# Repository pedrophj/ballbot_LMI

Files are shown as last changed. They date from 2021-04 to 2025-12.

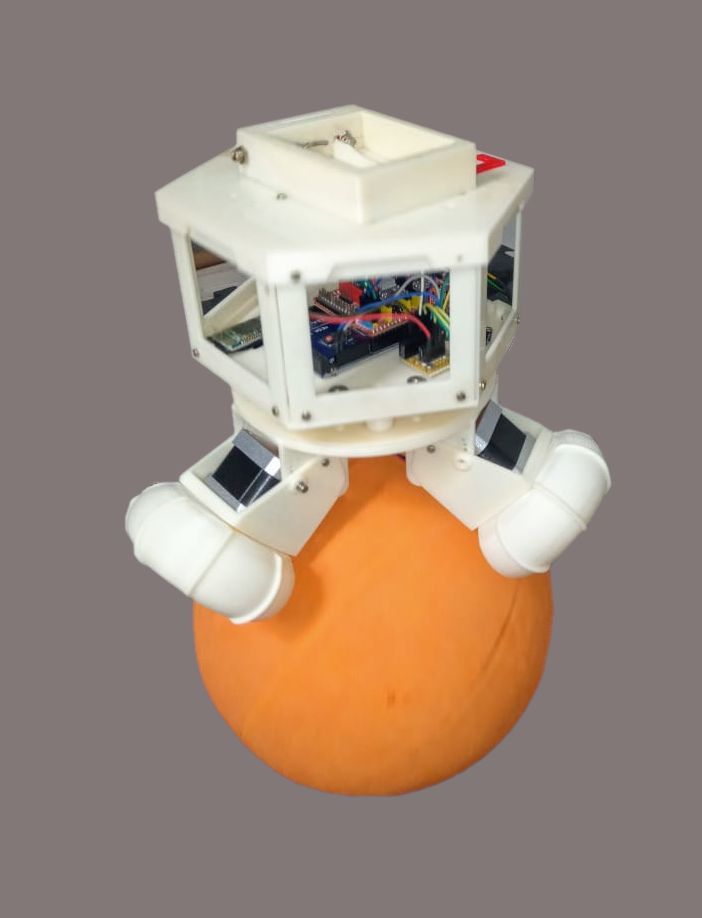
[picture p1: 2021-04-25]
MATLAB Simulink/ballbot_LMI.png

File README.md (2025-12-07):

# Design and Experimental Validation of a Ballbot: A Self-balancing Omnidirectional Robot

**Author**: Pedro Henrique de Jesus (pedro.jesus@sp.senai.br), ITA / SENAI 

**Advisors**: Cairo L. Nascimento Jr. (cairo@ita.br), Douglas Soares dos Santos (dsoares@ita.br), ITA.

## Abstract:
The files and codes presented in this repository refer to the construction of the ballbot robot. This robot rides on top of a basketball, and falls into a recent category of omnidirectional robots. In addition to the construction, files are available for the implementation of the camera location system, autonomous waypoint navigation and object tracking system.

ballbot 2

## Prerequisites for running MATLAB files:
- MATLAB R2015a

## Prerequisites for recording the embedded system:
- Arduino IDE equal to or greater than version 1.8.7
- Arduino Mega board

## Prerequisites for running the files in Python:
- Python 3.5.2 or higher
- numpy package installed with version 1.17.3 or higher
- OpenCV package installed with version 4.1.1.26 or higher

## Prerequisites for running the ballbot in the 3D simulator:
- CoppeliaSim version greater than or equal to 4.1.1

## File organization
- Files for 3D printing
  - Folder: mechanical
- Simulators
  - Folders: MATLAB Simulink and 3D simulator
- Embedded system
  - Folder: Arduino program
- Software for autonomous waypoint navigation
  - Folder: Control software
- Videos of real experiments and simulation
  - Folder: Videos
- My_Publications
  - Dissertação_Ballbot_Pedro_HJ.pdf: PDF of the master's dissertation
  - Artigo SysCon 2024: Design and Experimental Validation of a Ballbot: A Self-balancing Omnidirectional Robot.pdf
  - Folder: Presentation

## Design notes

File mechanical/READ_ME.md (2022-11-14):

List of printable files

To print a ballbot structure:
    
    Number          File 
      1             robo_tampaInferior.stl
      1             robo_tampaSuperior.stl
      1             robo_disco.stl
      6             robo_janela.stl
      3             robo_suporteMotor.stl
      3             robo_suporteMotorDisco.stl
      3             robo_paralama.stl
      3             robo_apoioDisco.stl
      
To print a ballbot wheel:
    
    Number          File 
      6             roda_roleteMenor.stl
      6             roda_roleteMaior.stl
      1             roda_garfo.stl
      1             roda_disco.STL
      1             roda_discoMotor.STL

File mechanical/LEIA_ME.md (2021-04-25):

Lista de arquivos para impressão.

	Para imprimir uma estrutura do ballbot:
    
    Quantidade      Arquivo 
      1             robo_tampaInferior.stl
      1             robo_tampaSuperior.stl
      1             robo_disco.stl
      6             robo_janela.stl
      3             robo_suporteMotor.stl
      3             robo_suporteMotorDisco.stl
      3             robo_paralama.stl
      3             robo_apoioDisco.stl
      
    Para imprimir uma roda do ballbot:
    
    Quantidade      Arquivo 
      6             roda_roleteMenor.stl
      6             roda_roleteMaior.stl
      1             roda_garfo.stl
      1             roda_disco.STL
      1             roda_discoMotor.STL

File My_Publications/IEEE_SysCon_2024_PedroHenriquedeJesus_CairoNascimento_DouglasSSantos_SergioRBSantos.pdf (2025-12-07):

# Design and Experimental Validation of a Ballbot: A Self-balancing Omnidirectional Robot

Pedro Henrique de Jesus∗
, Cairo Lucio Nascimento J ´ | unior ´

†
,
Douglas Soares dos Santos†
, Sergio Ronaldo Barros dos Santos ´

‡
∗ Servic¸o Nacional de Aprendizagem Industrial (SENAI), Pindamonhangaba-SP, Brazil Email: pedro.jesus@sp.senai.br
†
Instituto Tecnologico de Aerona ´ | utica (ITA), S ´ | ao Jos ˜ | e dos Campos-SP, Brazil ´
Emails: {cairo, dsoares}@ita.br
‡ Universidade Federal de Sao Paulo (UNIFESP), S ˜ | ao Jos ˜ | e dos Campos-SP, Brazil ´
Email: sergio.ronaldo@unifesp.br

Abstract—This article presents the design, modelling and control of a Self-balancing Omnidirecional Robot, also known as ballbot, for performing autonomous navigation (path following) and object tracking in structured environments using vision feedback. A real ballbot has unstable and non-linear dynamics with second-order constraints, and is classified as an underactuated system. These features require the implementation of a robust and efficient embedded control system for allowing the realization of attitude and navigation control. In this context, the development of this work was divided into six stages: 1) design and mechanical construction of the omnidirectional wheels and chassis using a 3D printer; 2) mathematical modeling of the prototype developed in Matlab/Simulink and creation of a realistic simulated model in CoppeliaSim simulator; 3) design of LQR and P/PI controllers to control X and Y position and orientation respectively using the mathematical model; 4) evaluation of designed controllers using the realistic model developed; 5) implementation of the controllers in the embedded system and integration with inertial sensors and actuators; 6) experimental validation of the proposed control system for autonomous navigation and object tracking. The experimental results have shown that the developed ballbot is able to perform path following and object tracking efficiently.

I. INTRODUCTION

A Self-balacing Omnidirectional Robot (Ballbot) is a mobile robot that incorporates the characteristics observed in an inverted pendulum which is balanced and moved on top of a sphere [1].
A Ballbot has numerous potential applications in several sectors of our society, such as working cooperatively in domestic and industrial environments transporting loads, acting as an information assistant in malls and hospitals, assisting senior citizens in sit-to-stand and walking movements, guiding leading visually impaired people in an unknown environments, autonomously mapping outdoor and indoor environments, performing mobile target tracking, and remote monitoring of large facilities.
One of the first ballbots was created in 2005 specifically to study the problem of dynamically unstable robots with a single point of contact with the ground [2]. The ballbot might carry out agile movements due to the ball rolling action and has inherently nonlinear unstable dynamics caused by the inverted pendulum. Unlike statically stable robots, dynamically unstable robots can accelerate and decelerate quickly and suffer a greater influence of gravity. This feature requires that the control system should effectively deal with the instability and nonlinearities that exist in this type of robot [3].
However, since a ballbot has unstable and nonlinear dynamics with second-order constraints and is classified as an underactuated system, designing effective attitude and navigation controllers for it is definitelynot a trivial task [4], [5]. This work aims to describe the development phases for designing, modeling and control of a ballbot used to perform autonomous navigation and object tracking in structured environments using inertial and vision sensors.
Initially, the robot chassis and its omnidirectional wheels were built using a 3D printer. Considering the robot physical parameters, including the power limitation of the motor drive power, 2 simulation models were developed: a mathematical model for Matlab/Simulink and a more realistic model for the CopelliaSim robot simulator. Using the mathematical model, the LQR and P/PI controllers were designed and tuned to control X and Y robot speed/position and orientation. Then they were evaluated using the realistic model in CoppeliaSim. For autonomous navigation, the ballbot receives its 3D position computed by an external vision system allowing it to follow the desired path defined by a set of waypoints positioned in its environment. For object tracking the ballbot uses an embedded camera to detect and locate the target object in relation to its own position. Then the vision based controller uses this informationto generate the control signals to the wheel actuators.
The main contribution of this work is to present a methodology for the construction of a ballbot, from the mechanical aspects to the implementation of the autonomous navigation and object tracking algorithms, including the experimental validation. The algorithms developed for this work and some demonstration videos are publicly available at https://github.com/pedrophj/ballbot LMI.
This article is organized as follows. Section II details the 2D model of the ballbot, as well as the parameters of the 3D simulation. Section III describes the methodology, constructive
2024 IEEE International Systems Conference (SysCon) | 979-8-3503-5880-3/24/$31.00 ©2024 IEEE | DOI: 10.1109/SysCon61195.2024.10553418

Authorized licensed use limited to: ITA - Instituto Tecnológico de Aeronáutica. Downloaded on August 19,2024 at 15:56:12 UTC from IEEE Xplore. Restrictions apply.

aspects and the control architecture. Simulation results for autonomous navigation and object tracking are presented in Section IV. And finally, conclusion and future works are described in Section V .

A. Related Works

In the last years, several studies were carried out for improving the stabilization control design of the self-balancing omnidirectional robot; however some few works present the complete stages of development of a ballbot, that goes from its mechanical structure to the implementation of the embedded control and guidance systems, allowing a full autonomous navigation and object tracking in indoor environments. Considering the existing literature about the path tracking and navigation, in the work of [6], the authors have only presented an attitude control for generating the velocity commands for the three wheels. In [7], a trajectory tracking approach based on waypoints for executing maneuver and avoiding collision with static and dynamic obstacles in cluttered environments is proposed. In [8], the authors have described an experimental trial to validate the control policies derived from the dynamic model and Dijsktra’s algorithm for surveillance and monitoring applications. In [9], a Fuzzy-based trajectory controller is proposed for performing the straight and circular motions in simulation. In [10], a Sliding Model Control (SMC) approach for trajectory tracking in simulation considering uncertainty and disturbance is proposed. In the [11], the authors have presented the design and implementation of a Fuzzy/PD controllers for controlling the attitude and tracking trajectories.
Regarding the mechanical and control system aspects, in the work of [12], the authors have presented the mechanical construction of a ballbot and modelling procedure using the Euler–Lagrange equations to derive the dynamic model. A Linear Quadratic Regulator with Integral (LQR + I) controller is proposed to keep the location around a point. In other work [5], the ballbot modeling and LQR controllers design to control the angular and X-Y position is proposed. However, the experimental validation is conducted using previously developed prototype.

II. BACKGROUND

In this section, we introduce all general aspects and some concepts employed throughout this work such as the used environment.

A. Ballbot Model

Figure 1 shows the simplified free body diagram of the ballbot represented by identical XZ and YZ planes. The free body diagram of the system is composed of a wheel (in orange), a rigid body (in blue) and a rod of length L used to connect the center of mass to the wheel. Note that X, Y and Z axes belongs to the inertial coordinate system whereas XB, YB and ZB axes composes the body coordinate system of the ballbot.

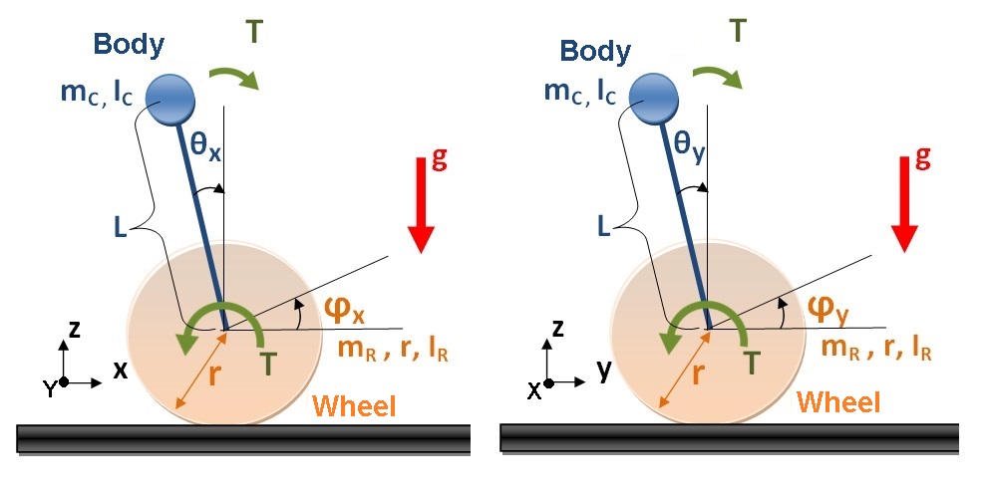
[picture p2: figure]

Fig. 1. Simplified ballbot planar model

Let be consider the angular acceleration on the sphere, wheel angle (φx) with respect to an initial horizontal reference point, and wheel angular velocity (φ˙x) as input of the simplified ballbot planar model and pitch (θx) angle measured in relation to the Y axis, angular velocity ( ˙θx) around the Y axis as output of the system. For describing the mathematical model, we use the parameters shown in Table I.
The nonlinear differential equations of the system is described in the form of a matrix as presented in eq. (1).

x˙1
x˙2
x˙3
x˙4

=

x2
mcgLsin(x1) + c1u + mcrLsin(x1)x

2
2
Ic + mcL

2 + mcrLcos(x1)
x4
−ru

(1)

where c1 = −Ir − (mr + mc)r

2 − mcrLcos(x1), u = φ¨, x1 = θx, x2 = ˙θ, x3 = x, and x4 = x˙.
It is assumed that the sphere is a rigid body and to be on contact with the ground without friction and slipping, and the wheel dynamics are disregarded due to their operation occurs at low angular speed.
The linearization of the nonlinear model is performed for an operating point that sets the angle change around the X and Y axes to be approximately zero. Thus, we can present the nonlinear ballbot plane model as a linear model in space states form.

x˙1
x˙2
x˙3
x˙4

=

0 1 0 0
24.84 0 0 0
0 | 0 0 1
0 | 0 0 0

x1
x2
x3
x4

+

0
−0.73
0
−0.12

u (2)

where x˙1, x˙2, x˙3 and x˙4 are the angular velocity observed on the body of the ballbot and u is the control signal.

B. Virtual Ballbot Model in CoppeliaSim
The simulator is an important tool for the control system design during the evaluation stage, since the system instability due to incorrect adjustment of the controllers might cause the ballbot to fall on the ground and consequently damage

TABLE I
PARAMETERS USED FOR MODELLING THE VIRTUAL BALLBOT
Parameter | Value | Unit
Acceleration of gravity | 9.81 | m/s²
Ball radius (r) | 0.12 | m
Ball mass (Mc) | 0.58 | kg
Moment of inertia of the sphere in X | 0.0134 | kgm²
Moment of inertia of the sphere in Y | 0.0134 | kgm²
Moment of inertia of the sphere in Z | 0.0134 | kgm²
Diameter of the cylindrical body | 0.2 | m
Height of the body (L) | 0.3 | m
body mass | 1.6 | kg
Moment of inertia of the body at X | 0.0413 | kgm²
Moment of inertia of the body in Y | 0.0413 | kgm²
Moment of inertia of the body in Z | 0.0720 | kgm²
Omniwheel diameter | 7 | cm
Omniwheel thickness | 1.3 | cm
Omniwheel mass | 50 | g
Omniwheel moment of inertia at X | 6.16 × 10⁻⁶ | kgm²
Omniwheel moment of inertia in Y | 6.16 × 10⁻⁶ | kgm²
Omniwheel moment of inertia in Z | 1.22 × 10⁻⁴ | kgm²

the actual prototype. In this work, we developed a virtual 3D model of the ballbot using the CoppeliaSim simulator to evaluate the performance of the stabilization and trajectory tracking controllers. This model reproduces the behavior of the dynamics observed in the real prototype with reliability and precision, taking into account disturbances such as wind and irregularities on the ground. Figure 2(a) shows the virtual ballbot developed for the CoppeliaSim simulator.
The attitude and position controllers are designed using the mathematical model described in Section II and are implemented in a script using the LUA language. This language allows to execute the control algorithms implemented in a script directly in CopelliaSim without using an external API. All the parameters shown in Table I are derived from the actual ballbot and are used to build the virtual model executed in CoppeliaSim. In CoppeliaSim each object in the scene can be edited separately, so that the dynamic properties of each part of the ballbot can be adjusted based on the values obtained from the prototype.

III. DEVELOPMENT OF THE SELF-BALANCING OMNIDIRECTIONAL ROBOT

A. Mechanical and Motor Aspects

The actual ballbot frame (Fig. 2(b)) is composed of a set of elements manufactured using a 3D printer and fixed using screws. The designed frame has a hexagonal shape with two layers for installing the on-board electronics, camera and battery. Each actuator is composed of a set of motor and omnidirectional wheel, positioned at 120º isometric angles and fixed to the frame using specifically designed supports. The positioning defined by the actuators allows eliminating non-holomonic movement restrictions, allowing the ballbot to execute displacement in X and Y directions (longitudinal and lateral movements) and around their own vertical axis.

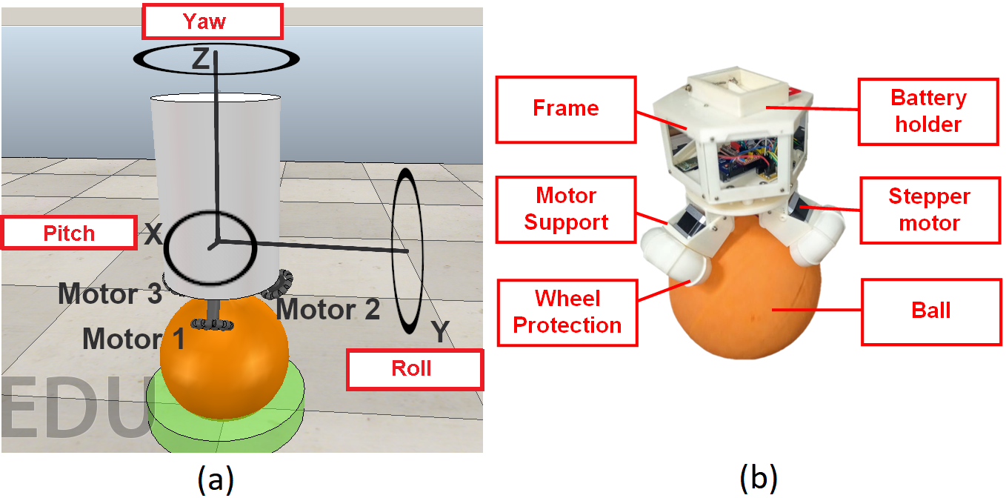
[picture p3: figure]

Fig. 2. Proposed actual and simulated Ballbot

(a) Model | (b) 3D printed

Fig. 3. Designed Omnidirecional Wheels

The motors are to be chosen to overcome the inertial imposed by the sphere, i.e., they must have enough torque to rotate the sphere producing an angular velocity that is translated into a linear velocity. The designed omnidirectional wheels (Fig. 3) have twelve 90 degree rollers symmetrically arranged to allow the ballbot to move along the Y axis and reduce body shake whereas conventional wheel rotation produces movement on the X axis.
The 4-wire bipolar stepper (NEMA 17, model 17HS4401) has 1.8 degree per step for smooth motion and requires a maximum current of 1.7A/phase for operation. This motor needs of 200 steps to complete a full 360 degree per turn and has a maximum load of 4.28 kg/cm. The angular speed of the motor depends on the frequency of the command generated by the drive in which affects the response of the platform to perform stabilization and holonomic displacement.
B. Embedded Electronics Systems

The ballbot uses a microcontroller (Arduino Mega) which it receives the acceleration and angular velocity measurements provided by the Inertial Measurement Unit (IMU) and the orientation given by the compass, and also generates the control signals of each of the motors through the drive DVR8825 composed of MOSFET transistors configured in two H bridges. The IMU and compass transmits the measurements performed using a I2C serial communication bus with a frequency of 100 kHz. Figure 4 presents the block diagram of the embedded electronic system implemented in the ballbot. Using bluetooth communication, the ballbot receives the relative position data calculated using the localization system and also the desired position references (waypoints) from the ground station computer for carrying out the navigation. On the other hand, the ballbot transmits the measurements realized by the IMU and compass, and also control signals generated by

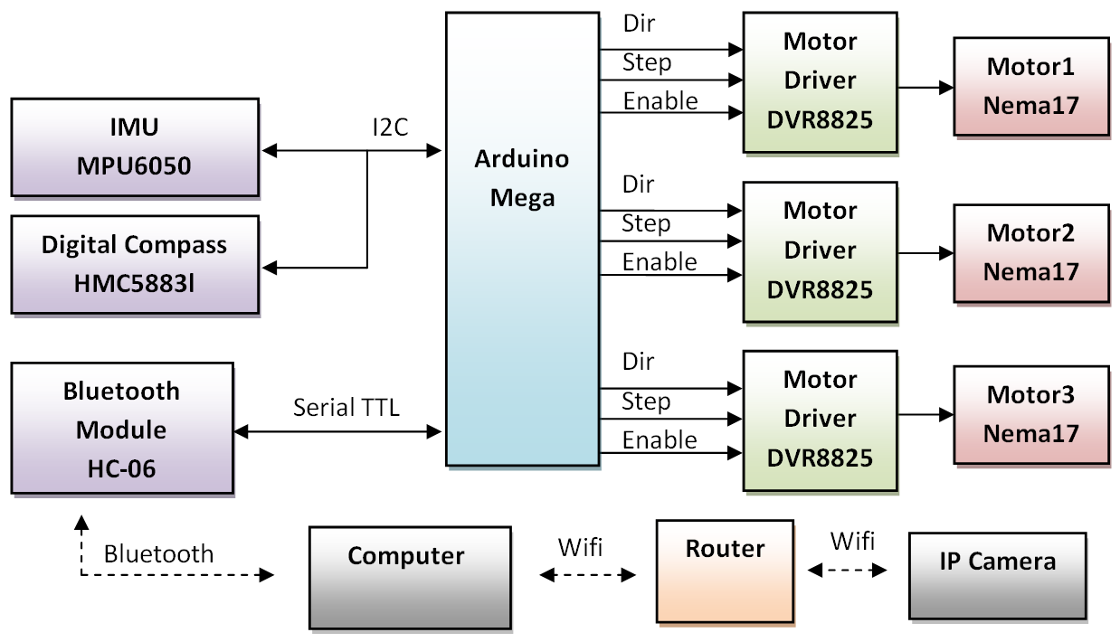
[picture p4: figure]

Fig. 4. Embedded system diagram

the motor drives using bluetooth communication (telemetry) to a ground station computer for user visualization.
The localization system uses the captured and processed images to estimate the position and velocity of the ballbot. An external camera captures the images from the environment and transmits the images for the ground station computer using a bluetooth connection.
C. Control System Architecture
The position control system denoted as XZ and YZ consists of two LQR controllers (Fig. 5) that are used to control the ballbot movements in relation to the X and Y axes on the global reference frame. The XZ controller takes the desired position (Xref ) or desired speed (X˙
ref ) of the ballbot as input signals whereas receiving the body angle (θx), angular speed of the body ( ˙θx), actual position (X), and ball speed (X˙
) in
the X direction. In turn, the YZ controller has as input signal (reference) the desired position (Yref ) or desired speed (Y ˙
ref )
whereas receiving the body angle (θy), angular speed of the body ( ˙θy), actual position (Y ), and ball speed (Y˙
) in the Y
direction.
The XZ and YZ controllers (Fig. 5) provide the control signals to command three ballbot actuators. The control outputs of the XZ and YZ controllers refer to the angular acceleration on the ball (Ax and Ay) and are computed using
(3) and (4).

Ax = θxK1 + ˙θxK2 + (X˙ − X˙ Ref )K3 + (X − XRef )K4 (3)

Ay = θyK1 + ˙θyK2 + (Y˙ − Y˙Ref )K3 + (Y − YRef )K4 (4)

where K = [K1, K2, K3, K4] is the gain vector for the LQR controllers.

The body orientation controller (yaw controller) consists of P/PI controllers that can be individually selected by the user to perform the rotation movement considering the response time and the expected accuracy for the desired angular position. The P/PI controller uses the yaw angle (Ψref ) or angular speed of the body (Ψ˙
ref ) as the desired reference whereas receiving the measured Yaw (ω) and Yaw rate (ω˙ ) signals of the ballbot. From the defined P/PI control law, the controller computes the

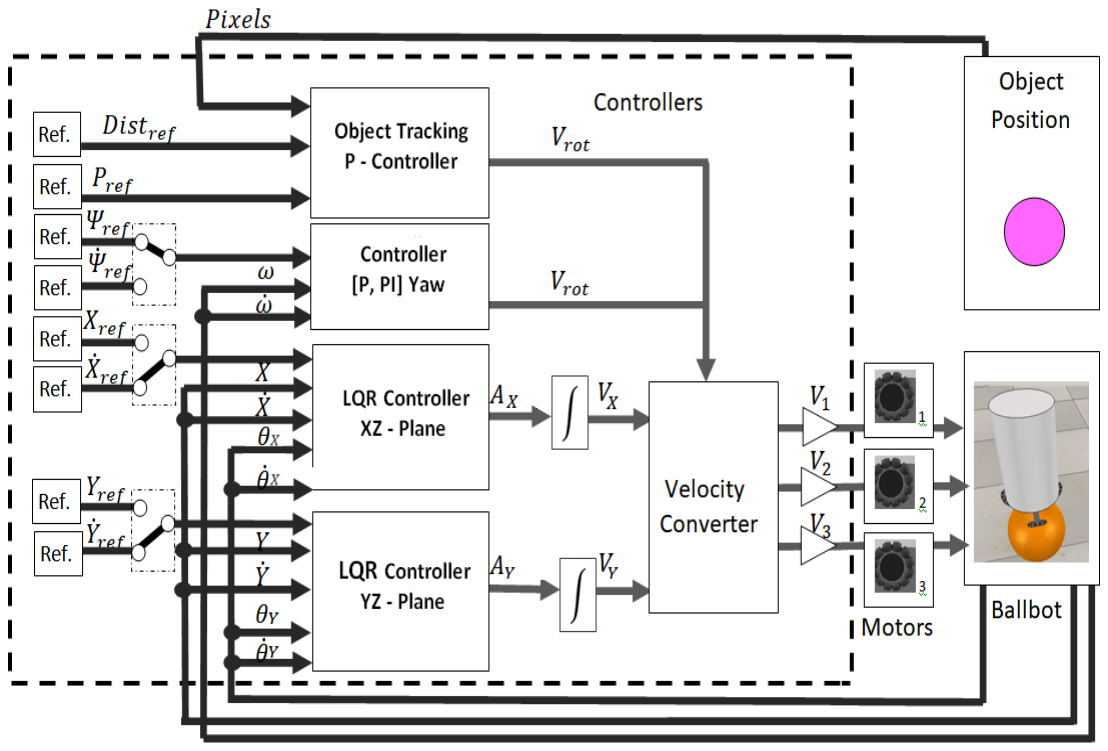
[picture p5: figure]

Fig. 5. Ballbot control system

control signal Vrot in which refers to the command of angular speed of the ballbot.
The actuation commands (Vx) and (Vy) are obtained from the output provided by the XZ and YZ controllers using a numerical integration method. A conversion module combines the actuation commands (Vx and Vy) relative to X and Y axes and also the body angular speed command Vrot to generate the rotation speed commands (V1,V2 and V3) for each of the engines. Using (5) , (6) and (7), the rotation speed commands are calculated as described in [6]. Note that the conversion module takes into account the angle and isometric position of the actuators.
V1 = −Vxcos(β) + Vrot | (5)
V2 = (0, 86Vx + 0.5Vy)cos(β) + Vrot | (6)
V3 = (−0, 86Vx + 0.5Vy)cos(β) + Vrot | (7)

where V1, V2 and V3 are the commands for driving each one of the engines and Vrot is the body angular speed command and Vx and Vy are the actuation commands relative to X and Y axes provided by the XZ and YZ controllers.
1) Complementary Filter and Computer Vision: The attitude of the ballbot (θx and θy) is computed using an Inertial Measurement Unit (IMU) consisting of a three-axis accelerometer, and a three-axis gyrometer. Through a complementary filter, the Pich and Roll angles may be calculated from the measurements performed by the accelerometer and gyrometer. This method allows eliminate the problem of bias error caused by numerical integration. In addition to Pitch e Roll angles, the yaw angle of the ballbot can be measured through a digital compass.
The complementary filter (Eq. 8 and 9) consists of a combination of a low-pass filter and a high-pass filter which are used to obtain the measurements of θx and θy of the ballbat. The low-pass filter uses the angle measurements obtained by the accelerometer whereas the high-pass filter receives the measurements obtained by the gyrometer. Note that the variables (weights) defined for each one of the filters were empirically adjusted. The coefficient α must be set with a value in the range of 0.5 to 1. In this work, due to the high vibration produced by the omnidirectional wheels the variable α was adjust to (i.e, 99% for the measurements obtained by the gyrometer and 1% for measurements provided by the accelerometer).
θx ← α(θ + θgyrox) + (1 − α)θaccx | (8)
θy ← α(θ + θgyroy) + (1 − α)θaccy | (9)

where θx and θy are the filtered Pitch and Roll angles, respectively, θgyrox and θgyroy are the angles obtained by the gyrometer using a numerical integration method, θaccx and θaccy are the angles obtained by the accelerometer using a trigonometry approach and α is filter coefficient.
To estimate the position of the ballbot during navigation and object tracking, a computer vision approach was implemented. Using the OpenCV library, we create a function to define the color threshold by keeping only the color of interest. The captured image of the environment is distorted, thus it is necessary to apply the homography matrix to transform a trapezoidal image into a two-dimensional rectangular image. After filtering, the contour detection is perform to estimate the position by converting pixels to centimeters.
2) Tuning: To adjust the gains of the LQR controllers, we need to assign weights (10 and 11) to the matrices Q and
R. The Q matrix were chosen to give more importance to the Pitch and Roll angles, aiming to keep the robot balanced under the ball. The R matrix was tuned to consider the control action, so that the actuator responds quickly with less effort as possible. Controller gains are shown in Table II.

Q =

50 | 0 | 0 | 0
0 | 20 | 0 | 0
0 | 0 | 10 | 0
0 | 0 | 0 | 20

4X4

(10)

R = [50]1X1 | (11)

where Q matrix is the weights on the states and R matrix is the weights on the control input.

D. Guidance Control System

Waypoint navigation may be understood as the robot movement based on a list of points. Whenever the robot gets close enough to one waypoint (reaching a waypoint radius), the desired point changes to the next ones until reaching the last point, making the the robot completes the navigation.
The coordinate of each one of the waypoints is defined by (WX and WY ), and the waypoint radius is estabilished by (RW ). Thus, the Euclidean distance between the position of the robot and the next waypoint can be computed using (12)

TABLE II
BALLBOT PARAMETERS
Control | Gain
LQR (XZ, YZ) Simulation | K = -
−70.51 | −14.56 | 0.45 | 2.98
LQR (YZ,YZ) Experimental | K = -
−50 | −25 | 1.5 | 2.5
Yaw Proportional Control | Kp = 0.3
Yaw Velocity PI Control | Kp = 1, Ki = 0.05

and the orientation (Yaw angle - ψW ) may be calculated by (13).

d =

p
(WX + XB)

2 + (WY + YB)

2 | (12)

ψW = tan⁻¹

WY −YB
WX−XB
(13)

Algorithm 1 Waypoint navigation algorithm

// Initial setting

### 1 Rw ← 10 // Radius in cm of the waypoint

### 2 waypoints ← listRead(

′mission.txt′
)// Load waypoint list

### 3 i ← 1 // Counter to read waypoints

### 4 yawRef ← compassRead() // Read robot guidance

### 5 yawW rite(yawRef) // Send via bluetooth

### 6 while T rue do 7 Xb, Y b ← estimateP osition(

′

camera′
)

### 8 W x, W y ← waypoints[i] 9 ErroX ← W x − Xb 10 ErroY ← W y − Y b 11 d ← sqrt(ErrorX ∗ ErroX + ErrorY ∗ ErrorY ) 12 if abs(ErrorY ) > Rw then 13 if abs(ErrorY ) > 0 then 14 move(

′right′
)

### 15 end 16 if abs(ErrorY ) < 0 then 17 move(

′

lef t′
)

### 18 end 19 end 20 else 21 if abs(ErrorX) > Rw then 22 if abs(ErrorX) > 0 then 23 move(

′f orward′
)

### 24 end 25 if abs(ErrorX) < 0 then 26 move(

′

back′
)

### 27 end 28 end 29 else 30 move(

′stop′
)

### 31 end 32 end 33 if abs(d) <= RW then 34 move(

′stop′
)

### 35 if length(waypoints) == i then 36 break 37 end 38 else 39 i ← i + 1 40 delaySecond(1) 41 end 42 end 43 end

Algorithm 2 Algorithm for object tracking

// Initial setting

### 1 P ref ← width/2 // Position reference (pixels) 2 Kg ← 0.02 // Yaw gains 3 distRef ← 50 // Distance threshold [cm]

### 4 while T rue do

// Returns the position in X (pixels)

### 5 posX ← getXObject(

′

camera′
) // Returns the distance
of the object

### 6 dist ← getDistance(

′

camera′
) // Calculates error for
yaw control

### 7 errorP osX ← posX − P ref // Calculate the distance

error
8 | errorDist | ← | dist − distRef | // Calculates yaw
proportional controller

### 9 V rot ← errorP osX ∗ Kg // Send output controller via

bluetooth

### 10 sendOutput(V rot) if abs(errorP osX) < 10 then 11 if errorDist > 0 then 12 move(

| | ′start′
)

### 13 if errorDist < 0 then 14 move(

| | ′stop′
)

The implemented Algorithm 1 perform the guidance control of the ballbot by executing the forward, backward, left and right movements with constant speed during the navigation by the environment. The objective of the algorithm is to correct the position in relation to the Y axis and then X axis, until reaching the minimum distance of the waypoint radius.

E. Object Motion Tracking
The object tracking problem consists of keeping the robot pointing to a certain object detected using an on-board camera. Thus, if the object moves to the right, the robot must make the Yaw correction in order to keep the object in the center of the image. If the object moves away (reducing the size of the captured image), the robot must move forward, reducing the position error and keeping the ballbot at a certain distance from the object.
The ballbot detects the object and tracks their movement using the images processed through a color filter. The used camera was adapted of the cell phone model Samsung Galaxy J1 and attached to the top of the robot, and their connection to the Wireless network was made using the IP WebCam application.
Knowing the diameter of the colored marker (object to be tracked) and determining the diameter in pixels from the image, it can estimate the distance between the colored marker and the ballbot. The distance (14) between the object and the ballbot may be estimated from the polynomial approximation obtained by the least squares method.

D(x) = 0, 001x

3 + x, 171x

2 − 0, 928x + 201 (14)

where x is the distance defined by the pixels and D is the distance between the colored marker and the ballbot.
The object tracking is performed using the Algorithm 2, in which incorporates the control system presented in (Fig. 5) to

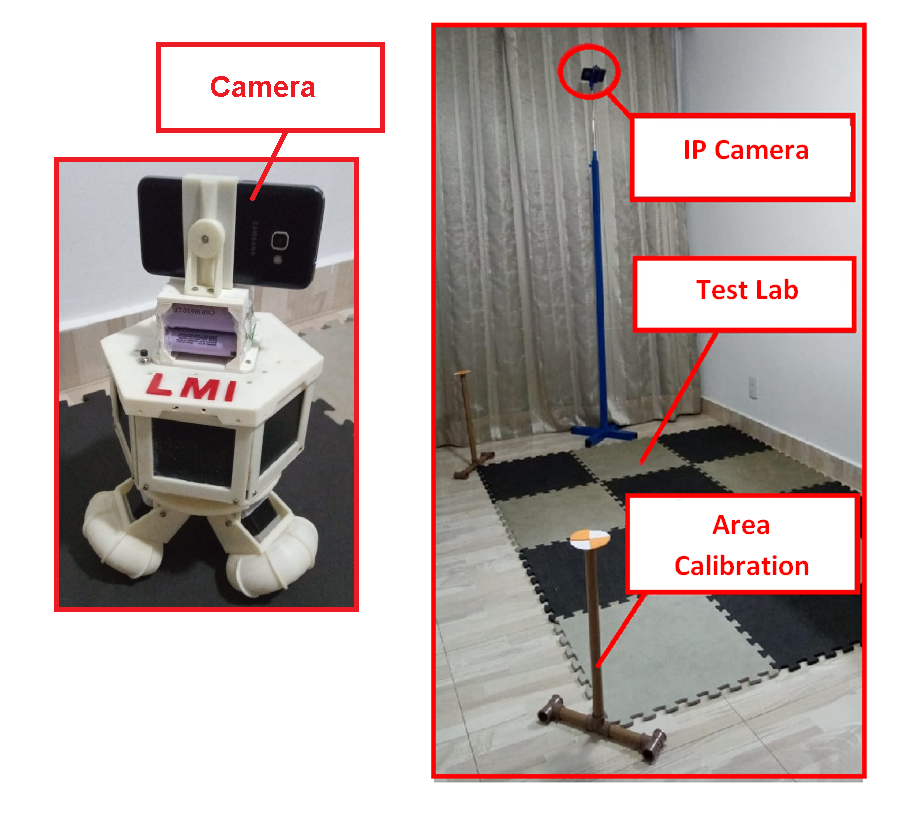
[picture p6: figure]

Fig. 6. Experimental Environment

perform the tracking. This tracking control is formed by the Yaw controller connected to the on-off position controller. The purpose of Yaw controller is to keep the colored object in the center of the image. Thus, this controller receive the pixels and the desired distance as input, and provides the output (rotation speed - Vrot) for the ballbot.

IV. RESULTS AND DISCUSSION
Figure 6 shows the proposed environment for performing the autonomous navigation using waypoints and tracking objects. A external IP camera attached on the tripod visualizes the navigation area delimited by the checkered floor.
In object tracking mode, the ballbot is equipped with a colored marker, with a different tone from the colors of the environment, to estimate the position of the robot. In object tracking mode, only a camera attached to the top of the robot is used. Using this camera, the ballbot can estimate the distance of the object and compute the object position on the global reference frame.
A. Evaluation in CoppeliaSim Simulator
The simulation of autonomous navigation performed in CoppeliaSim aims to validate the guidance algorithm, observing the attitude, X-Y position and angular speed of the actuators. Four points (waypoints) were defined to establish the path, given by the coordination [0, 100];[-50, 100], [-50, 0] and [0, 0]. In the simulation, the waypoints are defined in the script written in LUA by the user.
In the trajectory with 4 waypoints, the simulated robot completes the mission correctly (see Fig. 7(a)), where the waypoints 1, 2, 3 and 4 were reached in the time of 22 s, 32 s, 54 s and 65 s, respectively. Note that the ballbot arrives to the points 1 and 4 executing movements only in Y axis as seen in Fig. 8(a) (blue curve). At points 2 and 3, only the translation in X axis occurs, as seen in Fig. 8(a) (red curve). In both cause the robot navigates with constant speed.
It is important observe that the orientation of the ballbot was controlled to be 0, however the response presents some

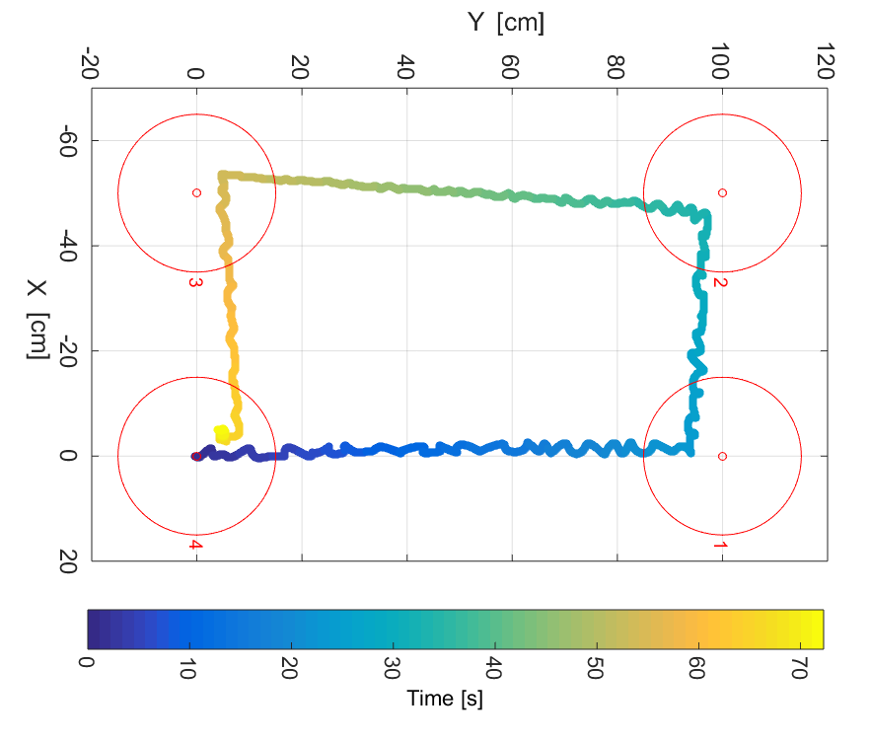
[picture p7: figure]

(a) CoppeliaSim simulation

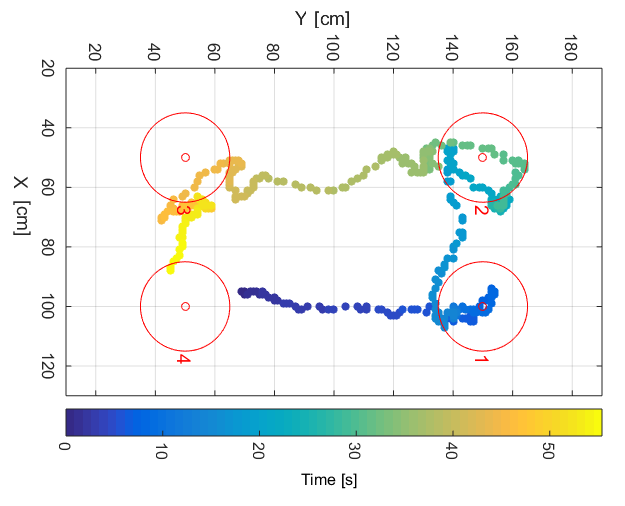
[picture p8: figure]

(b) Actual experimentation

Fig. 7. Ballbot navigation responses

small oscillations of 0.6 degrees around the desired reference. On the other hand, the pitch and roll angles present a larger oscillation due to the translational movements executed by the ballbot.

B. Experimental Validation
After evaluating the control and guidance algorithms in Simulation, we repeat the same assay using the experimental setup shown in Fig. 6. In the actual validation, the waypoints are defined by the user interface executed in the ground station and are sent to the actual ballbot using bluetooth communication.
The robot traveled the path to reach the four waypoints defined in the environment in 45 s as shown in Fig.7(b). This assay demonstrates the robustness of the control system design implemented to track the waypoints, and validates the methodology to construct the mechanical structure and actuators/omnidiretional wheels, including the localization algorithm using the adopted IMU and camera and also embedded firmware.
Figure 8(b) shows the X-Y position and actuator responses observed during the guidance execution to reach the four waypoints. Note that the speed spikes occur exactly during changing of the waypoints. This behavior occurs because of the ballbot needs to switch to the next waypoint at the moment that the ballbot arrives to the desired waypoint.

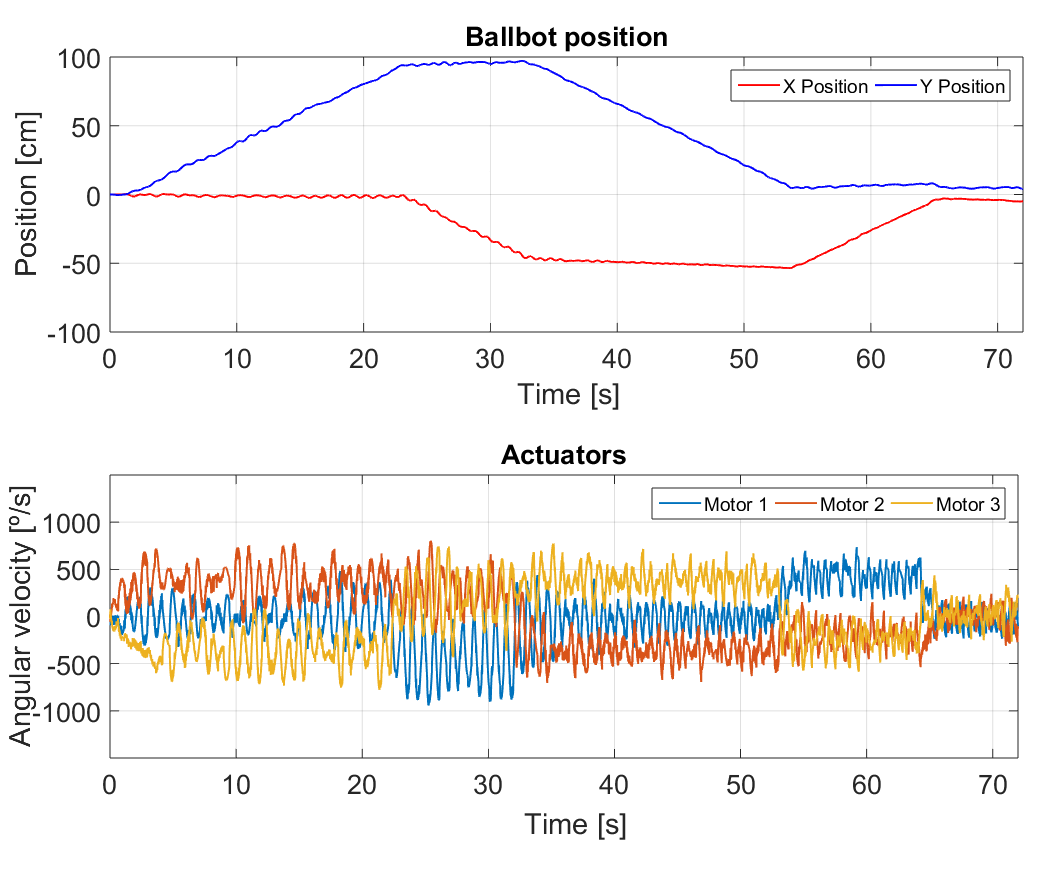
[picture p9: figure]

(a) CoppeliaSim simulation

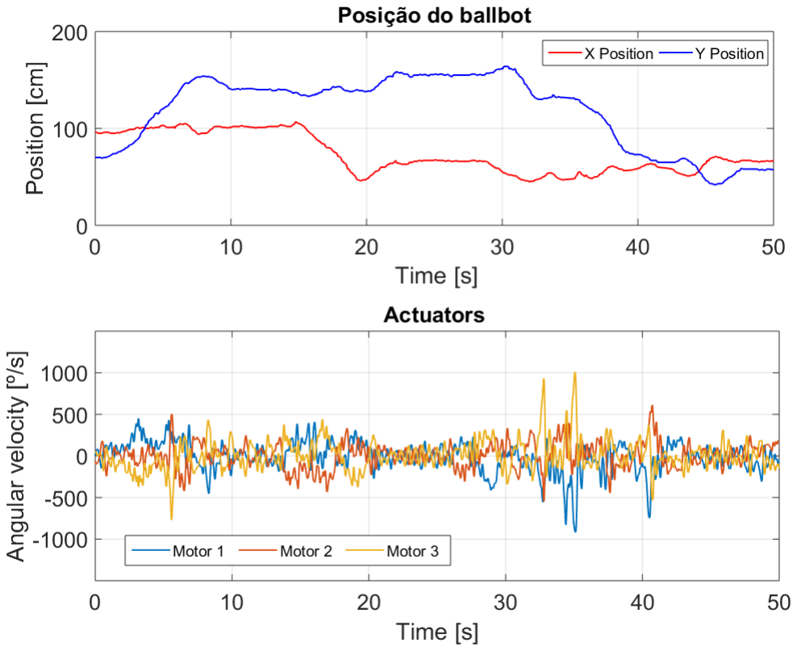
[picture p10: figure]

(b) Actual experimentation

Fig. 8. Ballbot position and actuators speed responses

During experimental validation, it was observed that the Yaw angle oscillated around 10 degrees. This behavior is caused by the vibration generated by the contact between the omnidirectional wheels and the irregular surface of the ball

C. Object Tracking

Figure 9 shows the experiment performed for tracking a colored object. In this test, the object is put at three different positions to validate the detection procedure and also the ballbot orientation control. The response of the Yaw (orientation) controller is obtained moving the object among three different positions with distance of 30 cm among them. The ballbot was positioned to keep the distance of 107 cm of the colored object. Initially, the ballbot points to the object in which is positioned at the central position (position 2, see Fig. 9), and then moving the object to the position 1 and 3, the ballbot must detect this object changing their orientation.
Figure 10 shows the experimental result obtained for tracking the colored object positioned in front of the ballbot. The object was kept 6 s at the position 1, and then it was placed by 13 s and 19 s at the position 2 and 3, respectively. Even proving an external disturbance on the ballbot, it can be observed that the ballbot can keep the object tracking (see 10), demonstrating that the designed orientation controller is robust and efficient.

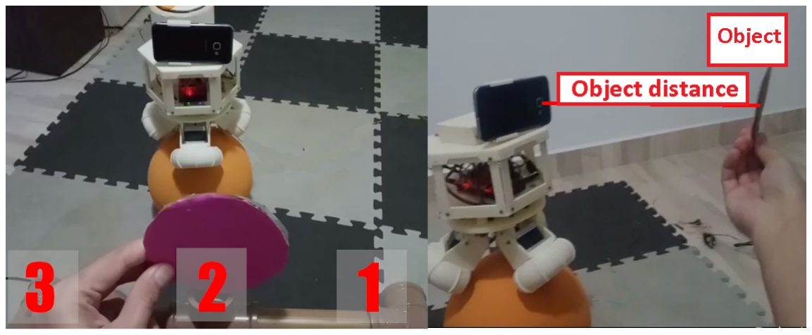
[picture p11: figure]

Fig. 9. Object tracking experimentation

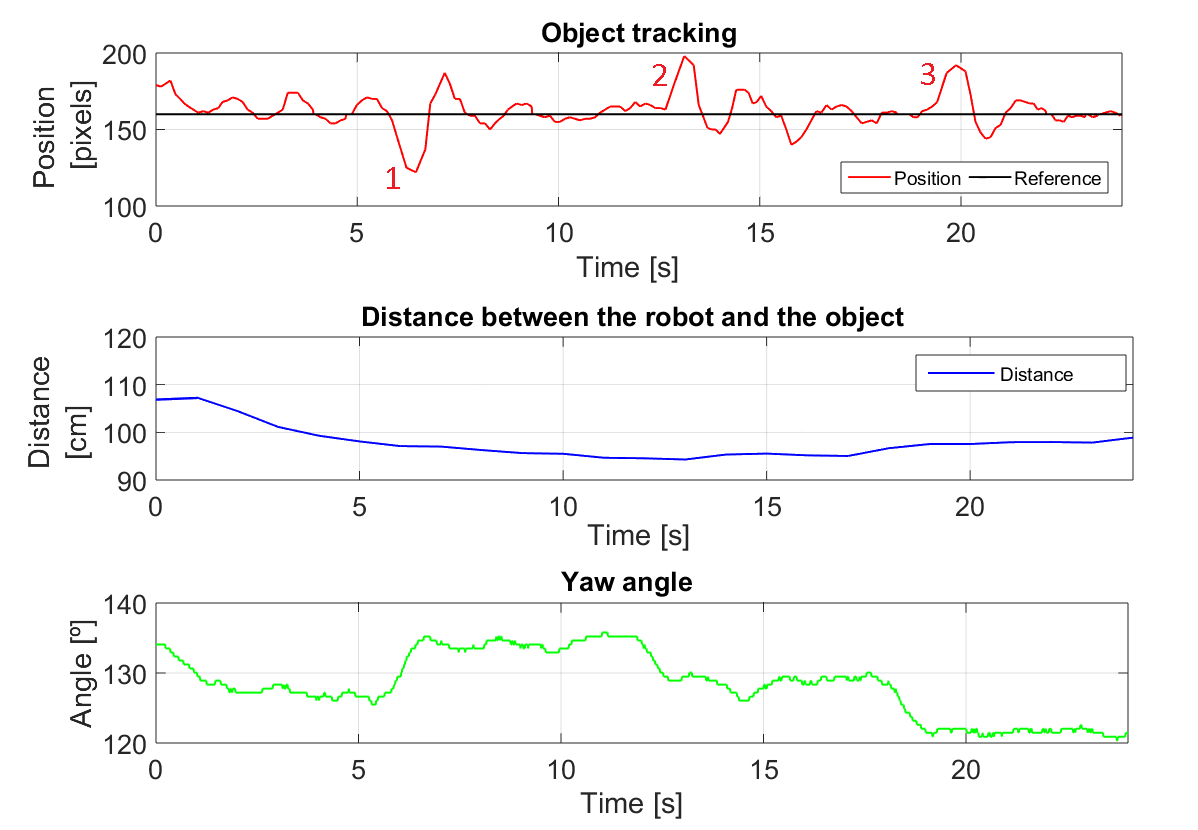
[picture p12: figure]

Fig. 10. Object tracking responses

D. Comparison Between Simulation and Experimental Results Regarding to the experimental results, it was observed that the ballbot responses presented greated oscilation whenever compared with the simulation. Note that the ballbot completes the mission in a shorter time in simulation compared to the actual trial. The observed actuators speed responses has similar behaviour in both tests, around 500º/s, but with different frequencies. Besides, in both testes, the small alteration of the moment of inertia affect the ballbot performance during the navigation, which must be compensated by the designed controllers.
The attitude response also presented similar small variation in simulation and experimental trials, reaching peaks of 3 to 8 degrees. In both, the observed variation is generated during the execution of the translational movement. Specifically to the Yaw response, the robot presented a small oscillation of 0.6 degrees in simulation whereas the maximum oscillation of 18 degree was noted in the actual trial.
V. CONCLUSION
A low-cost ballbot capable of performing the translation and rotation motions and executing different mission by navigating through waypoints was presented. The proposed methodology enables that the mechanical structure and omnidirectional wheels to be replicated using 3D printers. During the research development, it was observerd that the high friction produced by the rollers of the wheels hamper to control the the ballbot attitude. Another observed problem is relate to the range limitation of the camera to detect the colored marker. This restriction limits the size of the navigation area used to perform the experimental validation.
The simulation and experimental tests for autonomous navigation showed that the designed controllers are able to control the ballbot during the execution of their mission, navigating by the waypoints defined in the environment to by the user. The proposed solution to track the object based on the distance between the ballbot and the object have presented a reasonable performance for distances up to 2.5 meters. In addition, the position controllers demonstrated good performance, proving the ballbot’s ability to follow different path to reach the waypoints of interest or to detect a colored object.

ACKNOWLEDGEMENTS
The authors gratefully acknowledge the support for this research provided by FAPESP (Research Grants 2006/06005-0, 2016/04992-6 and 2024/01627-1), SENAI, ITA and UNIFESP.

REFERENCES

[1] T. Lauwers, G. Kantor, and R. Hollis, “A dynamically stable single-wheeled mobile robot with inverse mouse-ball drive,” in 2006 IEEE International Conference on Robotics and Automation (ICRA 2006), 2006, pp. 2884–2889. [Online]. Available: https: //dx.doi.org/10.1109/ROBOT.2006.1642139
[2] T. Lauwers, G. A. Kantor, and R. Hollis, “One is enough!” in 12th Proc. Int’l. Symp. on Robotics Research. San Francisco, CA, USA: IEEE, Oct. 2005, pp. 1–10. [Online]. Available: http: //www.msl.ri.cmu.edu/publications/pdfs/isrr05.pdf
[3] C.-W. Liao, C.-C. Tsai, Y. Y. Li, and C.-K. Chan, “Dynamic modeling and sliding-mode control of a ball robot with inverse mouse-ball drive,” in 2008 SICE Annual Conference, 2008, pp. 2951–2955. [Online]. Available: https://dx.doi.org/10.1109/SICE.2008.4655168
[4] J. W. van der Blonk, “Modeling and control of a ball-balancing robot,” Master’s thesis, University of Twente, 2014. [Online]. Available: http://essay.utwente.nl/65559/
[5] P. Fankhauser and C. Gwerder, “Modeling and control of a ballbot,” Bachelor Thesis, ETH, Swiss Federal Institute of Technology Zurich, 2010. [Online]. Available: https://doi.org/10.3929/ethz-a-010056685
[6] M. Kumagai and T. Ochiai, “Development of a robot balancing on a ball,” in 2008 International Conference on Control, Automation and Systems, 2008, pp. 433–438. [Online]. Available: https://doi.org/10.1109/ICCAS.2008.4694680
[7] M. Shomin, “Navigation and physical interaction with balancing robots,” Ph.D. dissertation, Carnegie Mellon University, Pittsburgh, PA, USA, 2016. [Online]. Available: https://doi.org/10.1184/R1/6720809.v1
[8] U. Nagarajan, G. Kantor, and R. Hollis, “Integrated planning and control for graceful navigation of shape-accelerated underactuated balancing mobile robots,” in 2012 IEEE International Conference on Robotics and Automation, 2012, pp. 136–141. [Online]. Available: https://doi.org/10.1109/ICRA.2012.6224970
[9] A. Lotfiani, M. Keshmiri, and M. Danesh, “Dynamic analysis and control synthesis of a spherical wheeled robot (ballbot),” in 2013 First RSI/ISM International Conference on Robotics and Mechatronics (ICRoM), 2013, pp. 481–486. [Online]. Available: https://doi.org/10.1109/ICRoM.2013.6510154
[10] S.-M. Lee and B. S. Park, “Robust control for trajectory tracking and balancing of a ballbot,” IEEE Access, vol. 8, pp. 159 324–159 330, 2020. [Online]. Available: https://doi.org/10.1109/ACCESS.2020.3020091
[11] C. Cai, J. Lu, and Z. Li, “Kinematic analysis and control algorithm for the ballbot,” IEEE Access, vol. 7, pp. 38 314–38 321, 2019. [Online]. Available: https://doi.org/10.1109/ACCESS.2019.2902219
[12] K. Sukvichai and M. Parnichkun, “Double-level ball-riding robot balancing: From system design, modeling, controller synthesis, to performance evaluation,” Mechatronics, vol. 24, no. 5, pp. 519–532, 2014. [Online]. Available: https://doi.org/10.1016/j.mechatronics.2014. 06.003

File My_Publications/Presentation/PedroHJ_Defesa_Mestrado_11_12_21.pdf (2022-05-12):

## Projeto, Construção e Testes de Um Robô Omnidirecional do Tipo Ballbot

Pedro Henrique de Jesus
Orientador: Prof. Dr. Cairo L. Nascimento Jr. Coorientador: Prof. Dr. Douglas Soares dos Santos

## Instituto Tecnológico de Aeronáutica

14/12/2021 | 1/55 /55

Sumário • | Introdução. • | Fundamentação: – História do ballbot

;
– Modelagem; – Controlador LQR; – Visão computacional; – Navegação por waypoints
- | Simulação: – Arquitetura de controle; – Resultados de simulação 2D; – Resultados de simulação 3D. • | Implementação: – Projeto e construção. • | Resultados Experimentais: – Controle de posição, velocidade e guinada; – Navegação autônoma; – Rastreamento de objetos. • | Conclusão e trabalhos futuros.

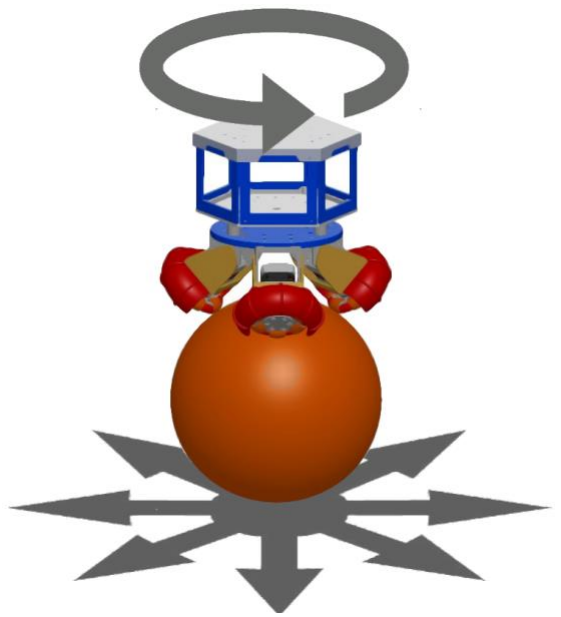
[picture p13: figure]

Motivação

- Categoria recente de robôs omnidirecionais.
- Capacidade de mudar a direção do seu deslocamento em espaços confinados.
- Implementação de navegação autônoma e rastreamento de objetos.

Introdução Fundamentação Simulação Implementação Resultados Experimentais Conclusão

Objetivo

Construir e testar o robô do tipo ballbot com a capacidade de seguir objetos, e também se locomover autonomamente em um ambiente supervisionado por câmeras.

Com esse propósito:

- Simular o modelo não linear do ballbot em duas e três dimensões;
- Testar os controladores: posição, velocidade, guinada e velocidade de guinada;
- Implementar um sistema de localização por câmera;
- Desenvolver um sistema de navegação por waypoints;
- Implementar um sistema de rastreamento por cor.

História do Ballbot

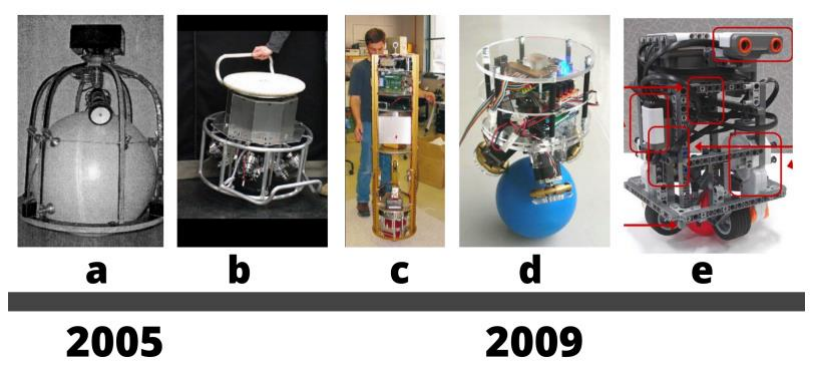
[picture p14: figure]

a) Havasi(2005), b) Endo e Nakamura (2005), c) Lauwers et al. (2005), d) Kumaga e Ochiai (2009) e
e) Yamamoto (2009)

História do Ballbot

a) Fong e Uppill (2009), b) Fankhauser e Gwerder (2010), c) Tsai et al. (2012), d) Sukvichai e Parnichkun (2014), e) Blonk (2014) e f) Yang et al. (2015).

Modelagem planar

onde:
mc = massa do corpo [kg]
Ic = momento de inércia do corpo [kgm²]
L = comprimento do centro da roda até o corpo [m] θx = ângulo do corpo (Arfagem) [º]
ϕx = ângulo da roda [º]
mR = massa da roda [kg]
IR = momento de inércia da roda [kgm²] r = raio da roda [m]
g = aceleração da gravidade [m/s²]
x = posição do robô

Modelo não linear na forma de espaço de estados

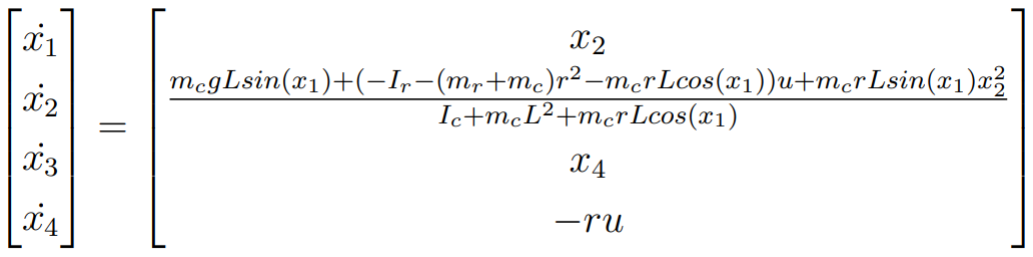
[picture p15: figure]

onde:

Modelo planar linearizado na origem do espaço de estados

A(t) | B(t)
onde:

Modelo planar linearizado na origem do espaço de estados

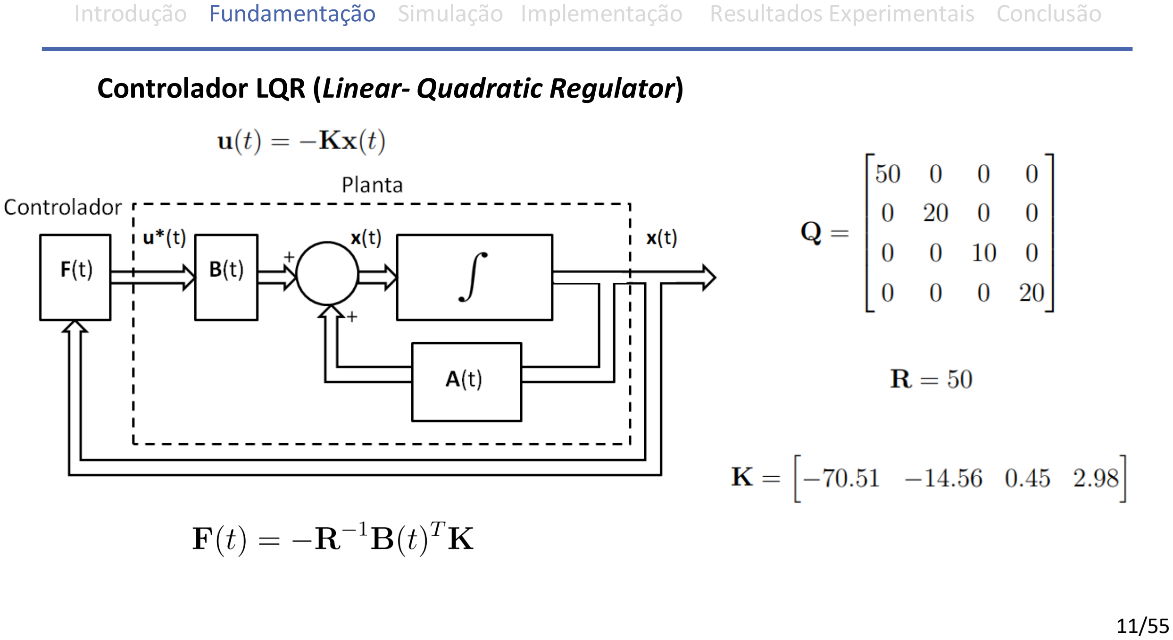
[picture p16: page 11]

Controlador LQR (Linear- Quadratic Regulator)

A(t)

+

+

Planta
Controlador
u*(t) | x(t) | x(t)
F(t) | B(t)

Visão computacional

Modelo pinhole

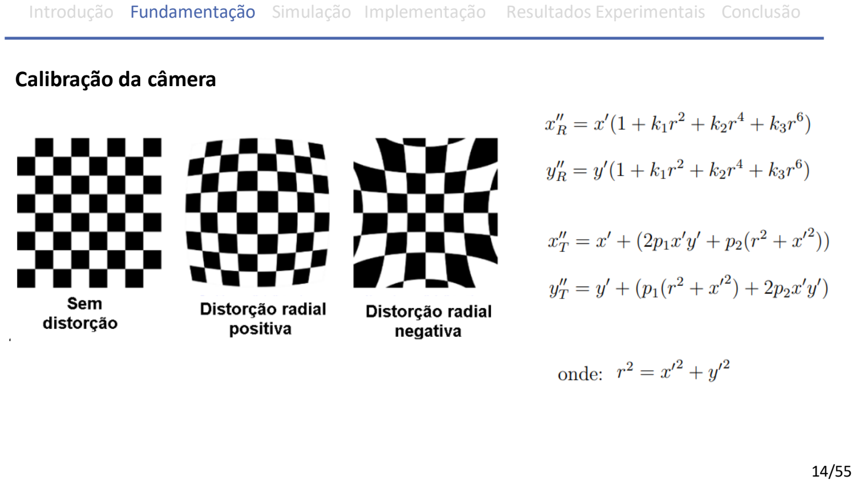
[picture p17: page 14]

Calibração da câmera

Uso do OpenCV para calibração

Método calibrateCamera permite calibrar usando imagens de chessboard

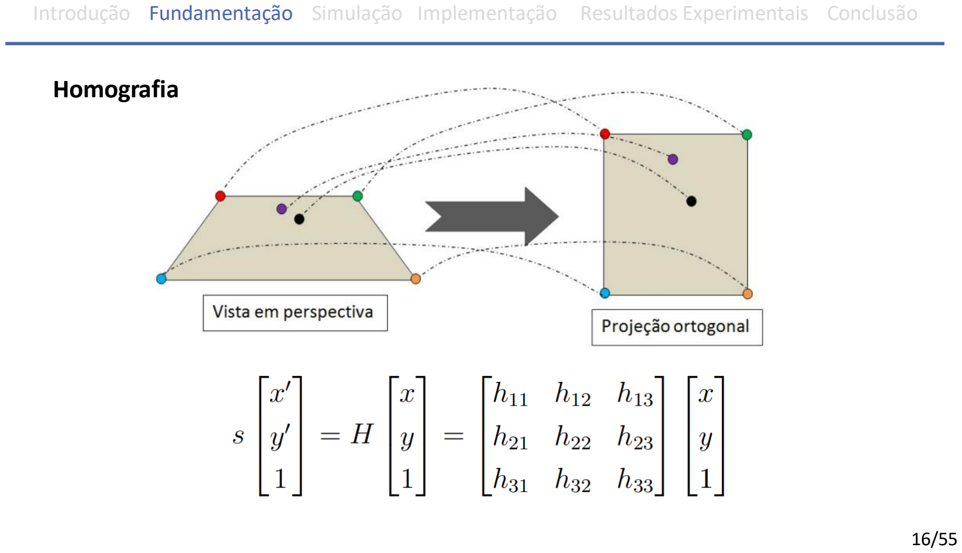
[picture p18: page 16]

Homografia

Navegação por waypoints

Neste tipo de navegação uma lista de waypoints é enviada para o robô seguir ponto a ponto. A missão é completada quando o robô seguir todos os pontos.

onde:
Rw = raio do waypoint [m]
WX, WY = posição do waypoint[m] ΨW = ângulo do waypoint [º]
XB, YB = posição do ballbot [m]
ΨB = ângulo do ballbot [º]
d = distância euclidiana entre o ballbot e o waypoint

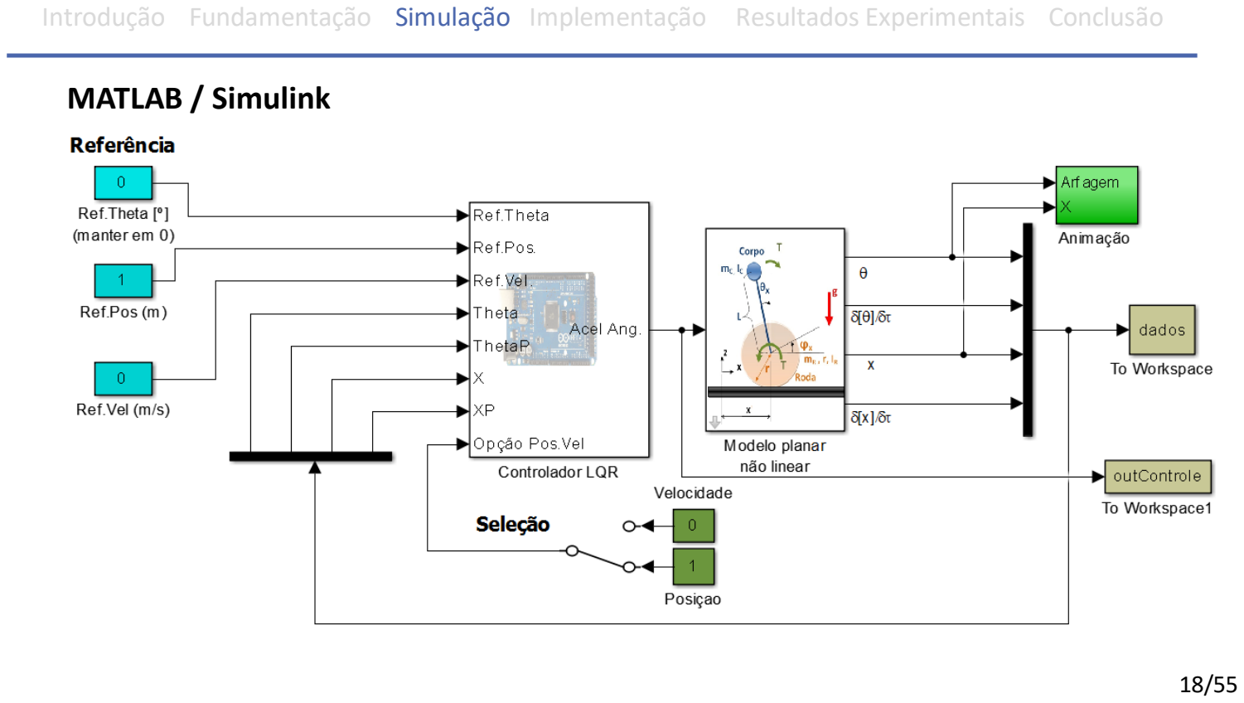
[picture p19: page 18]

MATLAB / Simulink

Bloco do modelo planar não linear

Bloco do controlador LQR

Resultados da simulação do modelo planar (MATLAB/Simulink)

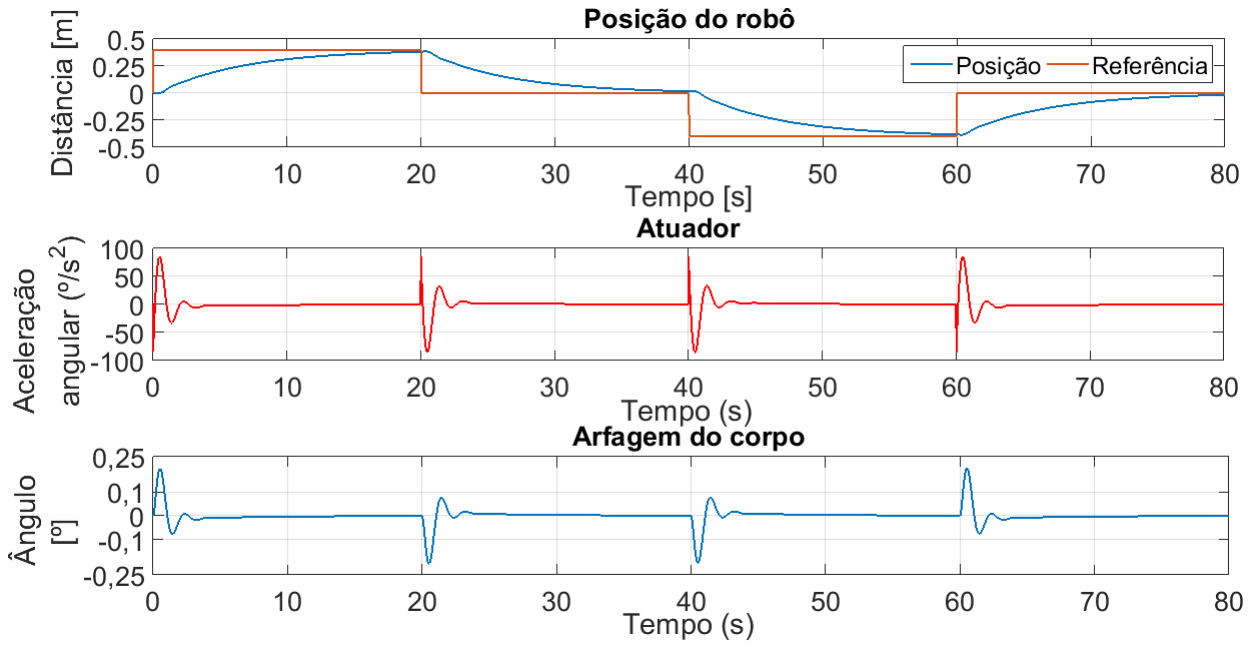
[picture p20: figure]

Resultados da simulação do modelo planar (MATLAB/Simulink)

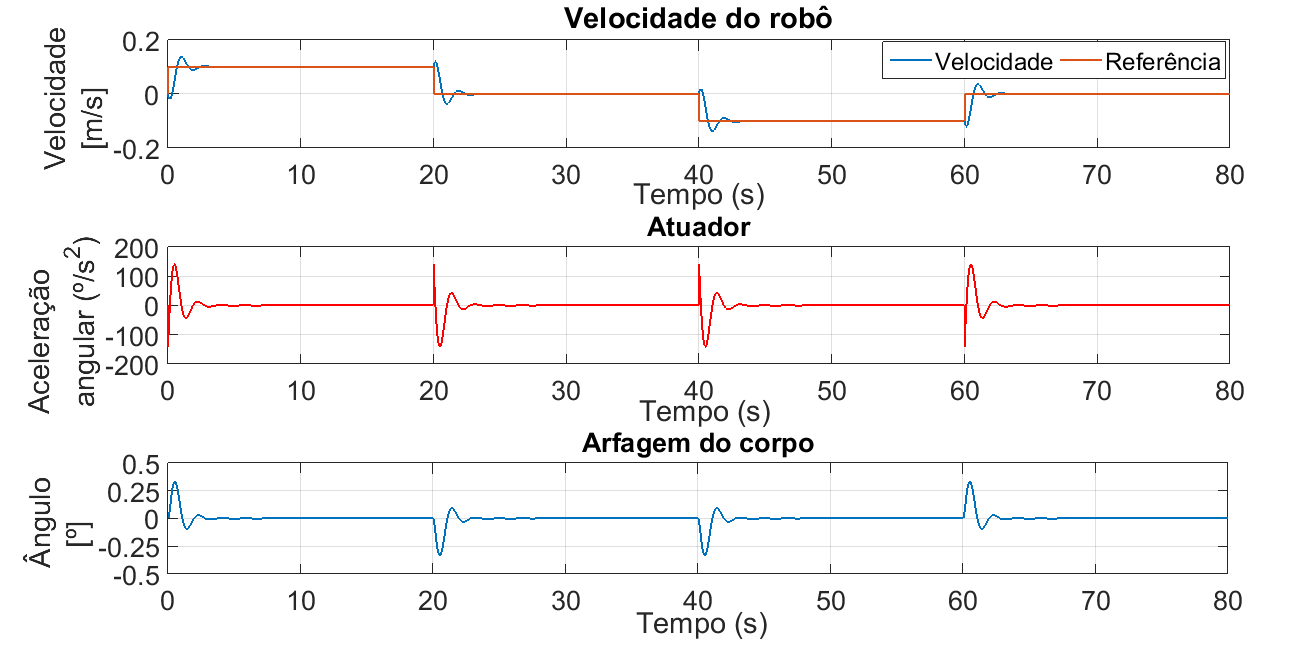
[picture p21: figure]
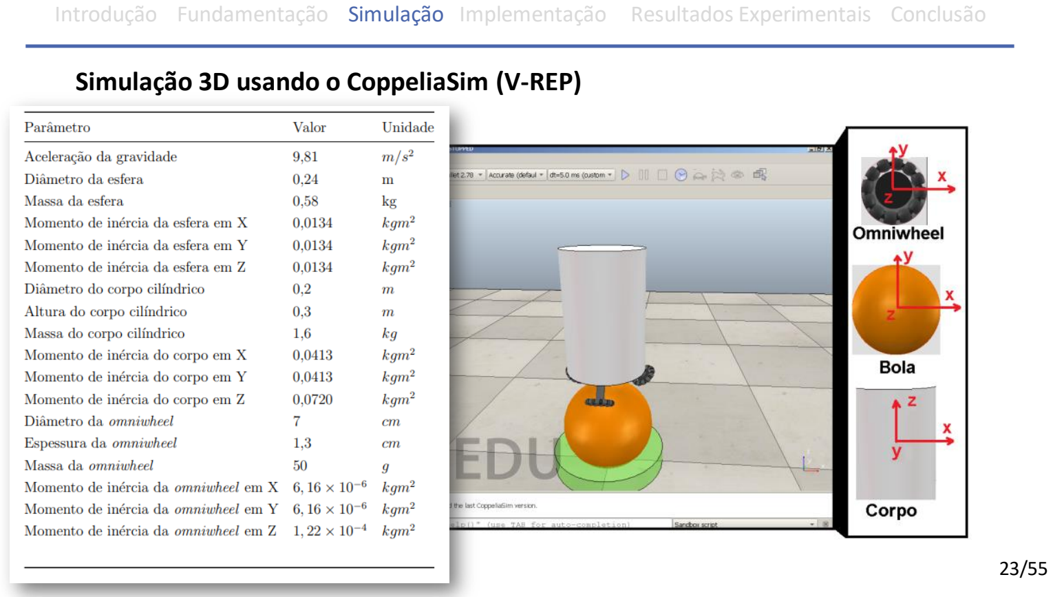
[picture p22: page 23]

Simulação 3D usando o CoppeliaSim (V-REP)

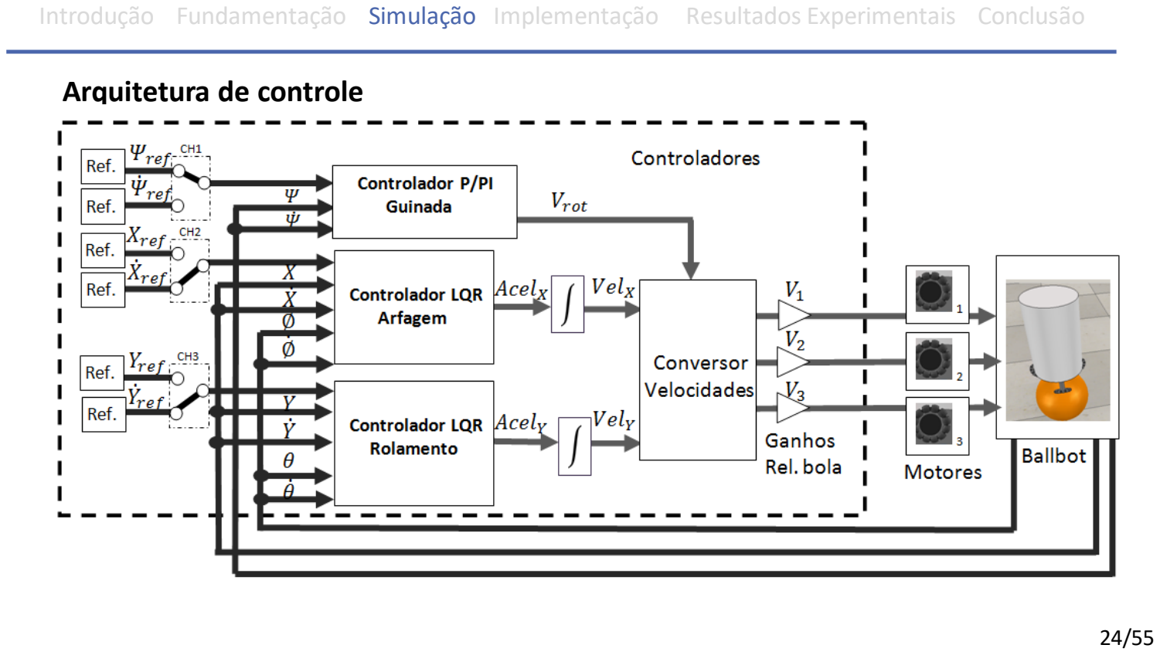
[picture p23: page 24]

Arquitetura de controle

Modos de operação

Conversão de velocidades

onde:

= velocidade de guinada;
= ângulo dos motores;
= velocidade dos motores;
= velocidade em x;
= velocidade em y.

Controle do ângulo de guinada, passo de simulação = 10 ms

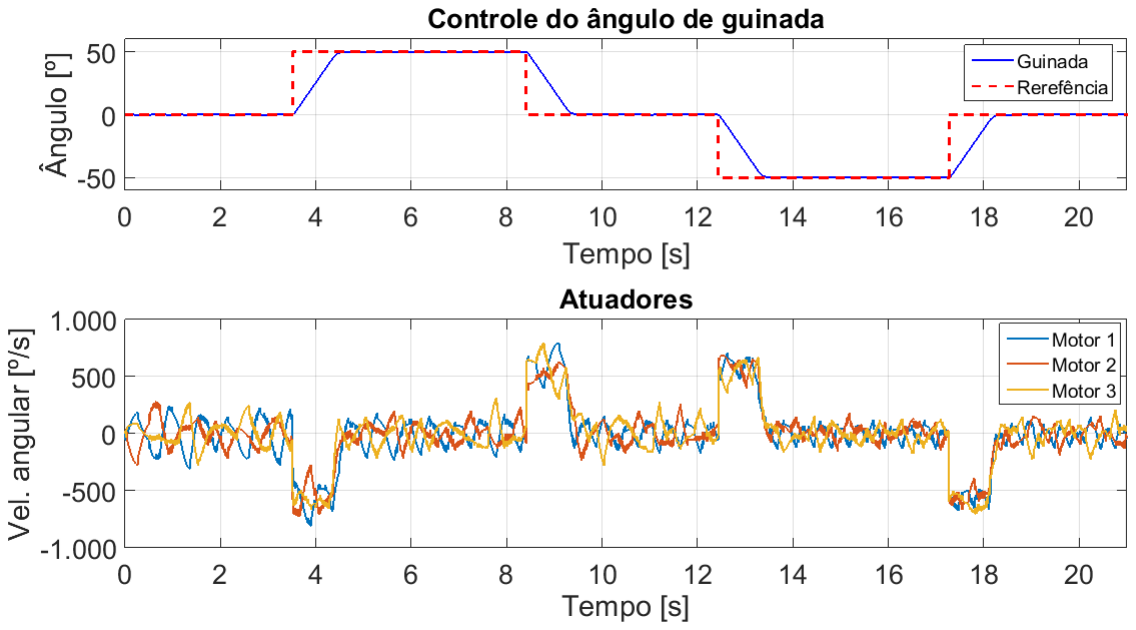
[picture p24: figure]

Controle de velocidade de guinada

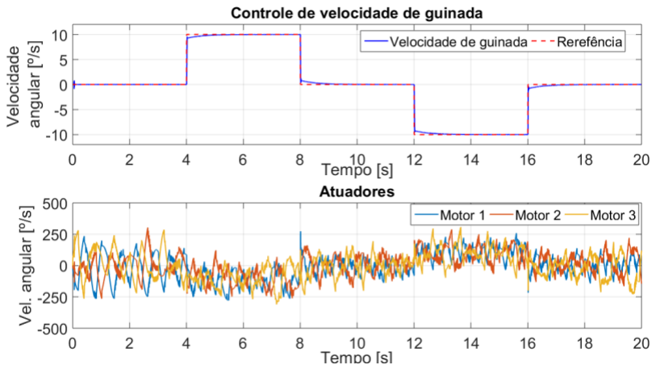
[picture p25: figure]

Controle de posição


Controle de velocidade

Navegação autônoma por waypoints

Algoritmo com prioridade de orientação | Robô com orientação fixa

Vídeo da navegação autônoma por waypoints no CoppeliaSim


Estrutura do robô Ballbot

Diagrama de blocos

Técnicas para melhorar o desempenho do sistema embarcado

- A taxa de comunicação serial entre o Arduino e o módulo Bluetooth foi aumentada para 115200 bps.
- Uso da interrupção de temporizadores do Arduino para gerar os sinais para os drivers de potência dos motores.
- Geração dos pulsos para os drivers de potência dos motores usando os pinos de saída dos registradores das portas do Arduino.
- Uso da técnica de deslocamento de bits para operações de multiplicação/divisão no programa executado no Arduino.

Detalhes da roda omnidirecional


θ = α(θ + θgyro dt) + (1- α) θgyro

onde:
θ = ângulo de arfagem filtrado [º]
θacc = ângulo obtido pelo acelerômetro [º] θgyro = ângulo obtido pelo girômetro [º]
α = constante do filtro
dt = passo de integração

Resultado do filtro complementar



Ambiente de testes


Software de controle

Controle do ângulo de guinada

Controle de velocidade de guinada

/55


Controle de posição

/55

Controle de velocidade

/55


Resultado da navegação por waypoints

/55

Vídeo da navegação autônoma por waypoints


Experimental

Rastreamento de objetos

Posição desejada do objeto é sempre no centro da imagem captada pela câmera embarcada.

Uso de filtro de cor para detectar o objeto colorido.

Primeiro o robô se orienta em relação ao objeto e depois executa o movimento de translação.

A estimativa de distância entre o ballbot e o objeto colorido foi feita com base no diâmetro do objeto.

Estimativa da distância entre o objeto e o robô

Experimento de rastreamento de objeto


Vídeos de rastreamento de objeto

Somente ação de guinada | Com ações de guinada e translação

Resultado do rastreamento de guinada


Considerações finais

Apresentou-se neste trabalho um ballbot de baixo custo capaz de executar translação e rotação, o que permite que o robô tenha a capacidade de executar uma determinada missão por meio da navegação por waypoints e também rastrear objetos.

Principais dificuldades:
- Construção de rodas omnidirecionais de boa qualidade;
- Ruídos causados pela vibração dos motores;
- Limitação da área útil de navegação;
- Baixo poder computacional do sistema embarcado.

Trabalhos futuros

Alguns pontos que podem ser explorados em trabalhos futuros:

- Construção de outros ballbots, para tarefas colaborativas;
- Uso de ballbot com SLAM (Simultaneous Localization and Mapping);
- Embarcar um LIDAR (Light Detection and Ranging) ou câmera de profundidade para a detecção de obstáculos;
- Navegação outdoor com o uso de GPS;
- Uso de uma ou mais câmeras para aumentar o ambiente de navegação.

Introdução Fundamentação Simulação Implementação Resultados Experimentais Conclusão

# Obrigado!

## Fim

ITA - Instituto Tecnológico de Aeronáutica

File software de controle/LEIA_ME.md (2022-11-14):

  Esse software foi escrito em Python 3 e precisa que seja instalado o módulo openCV.
  
  Baixe todos os arquivos para criar a GUI:  https://1drv.ms/u/s!AnCh2isdFBEugvgiTFld_0DegOptdw?e=OA4d3N

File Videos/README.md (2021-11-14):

| Arquivo | Descrição |
| :---: | :---: |
| experimento_controle_app.mp4 | Funcionamento do controle via *bluetooth*, com translação e guinada do *ballbot*|
| experimento_controle_guinada_app.mp4 | Funcionamento do controle de guinada via *bluetooth* | 
| experimento_navegacao_2.mp4 | Experimento de navegação autônoma por 2 *waypoints* | 
| experimento_navegacao_3.mp4 | Experimento de navegação autônoma por 3 *waypoints* | 
| experimento_navegacao_4.mp4 | Experimento de navegação autônoma por 4 *waypoints* | 
| experimento_navegacao_reta.mp4 | Experimento que o robô executa uma trajetória de uma reta | 
| experimento_rastreamento_guinada.mp4 | O robô com câmera embarcada rastreia um objeto colorido, somente guinada e sem translação | 
| experimento_rastreamento_translacao.mp4 | O robô com câmera embarcada rastreia um objeto colorido, com guinada e translação  | 
| navegacao_coppelia_19pontos.mp4 | Simulação no CoppeliaSim, onde o *ballbot* segue uma trajetória de formato "8", com 19 pontos | 
| navegacao_coppelia_4pontos_modo1.mp4 | Simulação no CoppeliaSim, onde o *ballbot* segue uma trajetória de 4 pontos, com permissão de variar a guinada  | 
| navegacao_coppelia_4pontos_modo2.mp4 | Simulação no CoppeliaSim, onde o *ballbot* segue uma trajetória de 4 pontos, com orientação fixa durante o trajeto todo | 

## Vídeos do Simulador CoppeliaSim

Os vídeos abaixo mostram a navegação autônoma com 4 *waypoints*, operando em dois modos. O modo 1 a referência de guinada é alterada com o objetivo do robô orientar em direção ao *waypoint* atual. O modo 2 o robô executa a missão com uma orientação fixa. 
As coordenadas dos pontos (em centímetros) foram: [ [0,100] , [-50,100] , [-50,0] [0,0] ].

- navegacao_coppeliaSim_4pontos_modo1.mp4
- navegacao_coppeliaSim_4pontos_modo2.mp4

A navegação de uma trajetória complexa em formato de "8" no modo 1 é apresentado no vídeo abaixo. As coordenadas dos pontos (em centímetros) foram: [ [0,0], [19.9, 7.7], [28.5,25.12],[20.9,42.7],[7.1 ,50.2],[-9.8,57.9],[-26,69.2],[-26.6,88.46],[-9.89,99.19],[10.3,98.3],[24.2,87.4],[24.4,71.9],[15.6,59.3],[0,55],[-22,43.3],[-30.6,36.6],[-31.7,22.7],[-23.4,8],[0,0] ].

- navegacao_coppeliaSim_19pontos.mp4

## Vídeos de rastreamento de objetos

No primeiro vídeo o robô deve seguir o objeto colorido, ou seja, o objeto deve estar sempre no centro da imagem captada pela câmera embarcada no robô. Nesse experimento o robô está a 1 metro de distância do objeto. A posição do objeto colorido é alterada em 3 etapas com distância total de 30 cm. O objetivo de analisar apenas a guinada do robô. No segundo vídeo é testado tanto a guinada como a translação.

- experimento_rastreamento_guinada.mp4
- experimento_rastreamento_translacao.mp4

## Vídeos de navegação por waypoints

Os vídeos mostram os resultados de navegação com 2, 3 e 4 *waypoints*. Essa lista é carregada em um arquivo .txt no software de controle e então é enviada via *bluetooth* para o robô. O *ballbot* deve seguir ponto a ponto até completar todos os pontos da lista. 

- experimento_navegacao_2.mp4
- experimento_navegacao_3.mp4
- experimento_navegacao_4.mp4
- experimento_navegacao_reta.mp4

As coordenadas dos pontos(em centímetros) foram: 
- 2 pontos: [[75,150],[75,50]]; 
- 3 pontos: [[100,150],[50,150],[50,50]]; 
- 4 pontos: [[100,150], [50,150], [50,50],[100,50]].

## Vídeos de controle via aplicativo

Os dois vídeos abaixo mostram o controle manual via *bluetooth*. No modo de guinada são incrementados as velocidades dos 3 motores. No arquivo experimento_controle_app a translação foi executada enviando a referência (10 cm/s) de velocidade via *bluetooth*.

- experimento_controle_guinada_app.mp4 
- experimento_controle_app.mp4

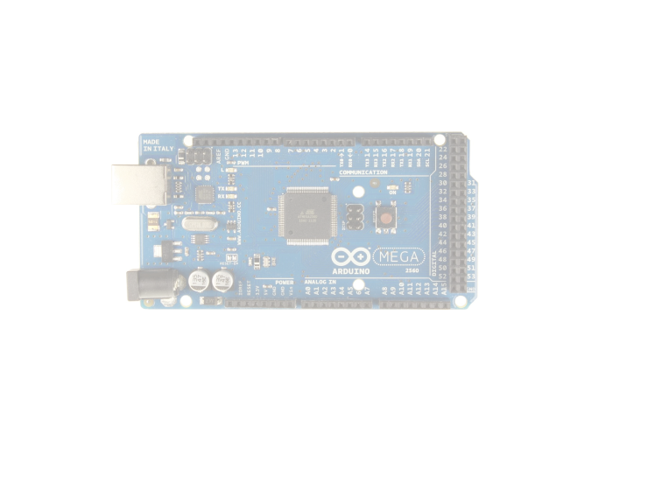
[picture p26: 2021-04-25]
MATLAB Simulink/ArduinoMega.png

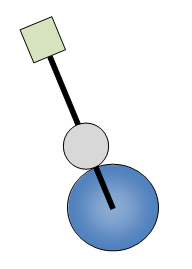
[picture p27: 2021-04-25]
MATLAB Simulink/ballbot_image.png

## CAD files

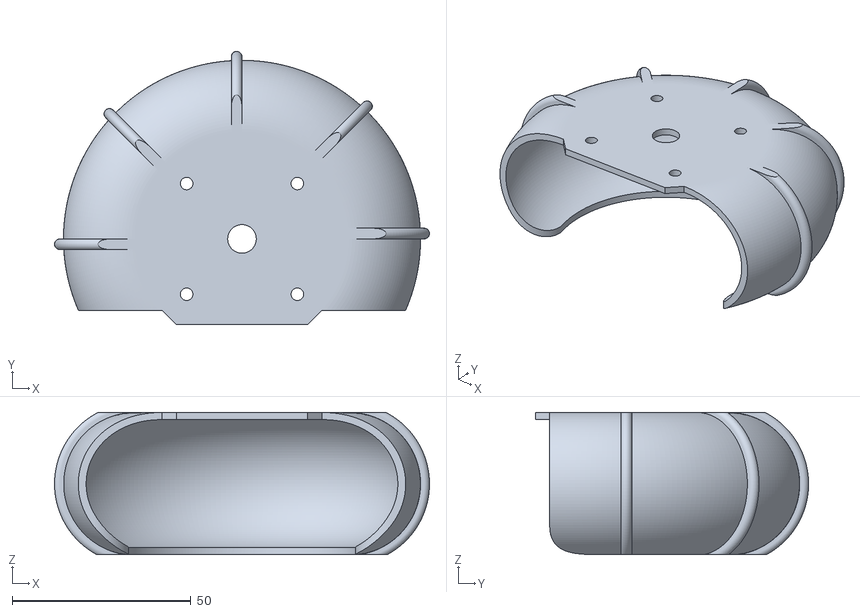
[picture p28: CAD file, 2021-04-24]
mechanical/robo_paralama.STL
105.0 x 76.5 x 39.8

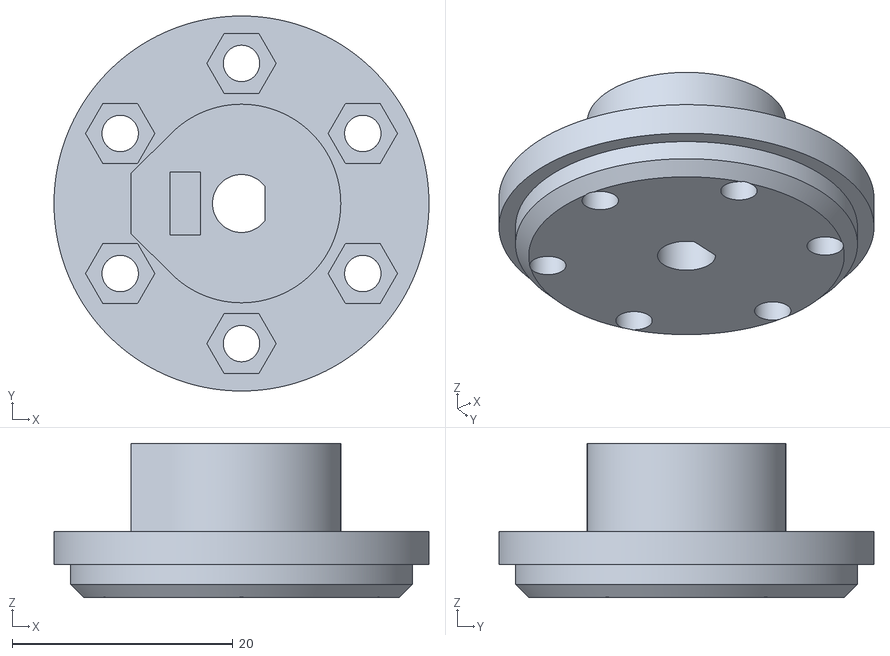
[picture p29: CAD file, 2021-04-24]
mechanical/roda_discoMotor.STL
34.0 x 34.0 x 14.0

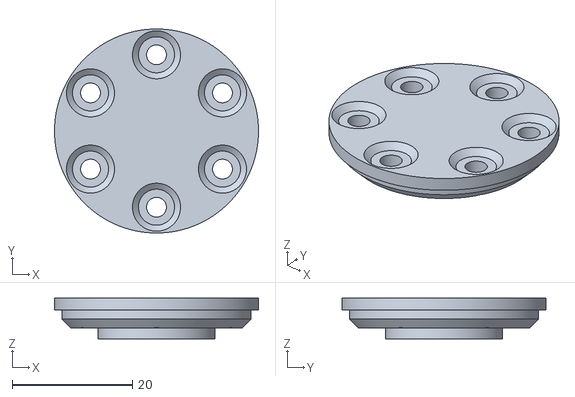
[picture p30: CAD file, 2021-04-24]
mechanical/roda_disco.STL
34.0 x 34.0 x 6.80

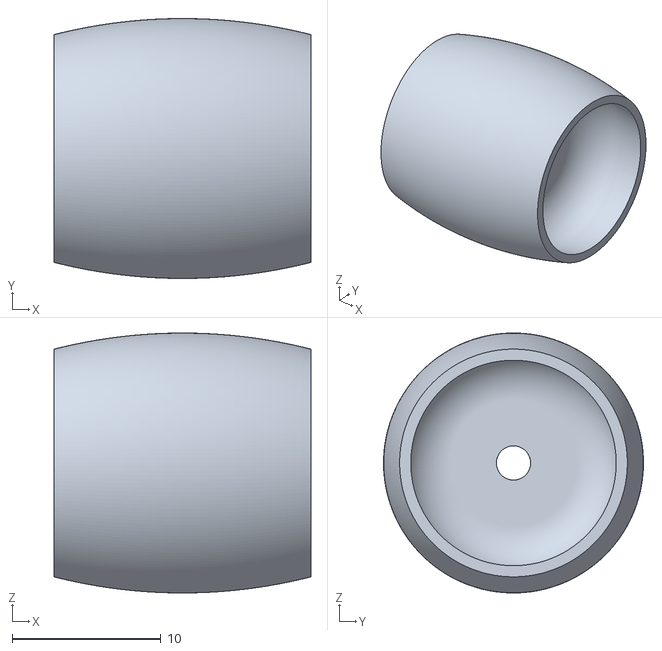
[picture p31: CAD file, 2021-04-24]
mechanical/roda_roleteMaior.STL
17.3 x 17.5 x 17.5

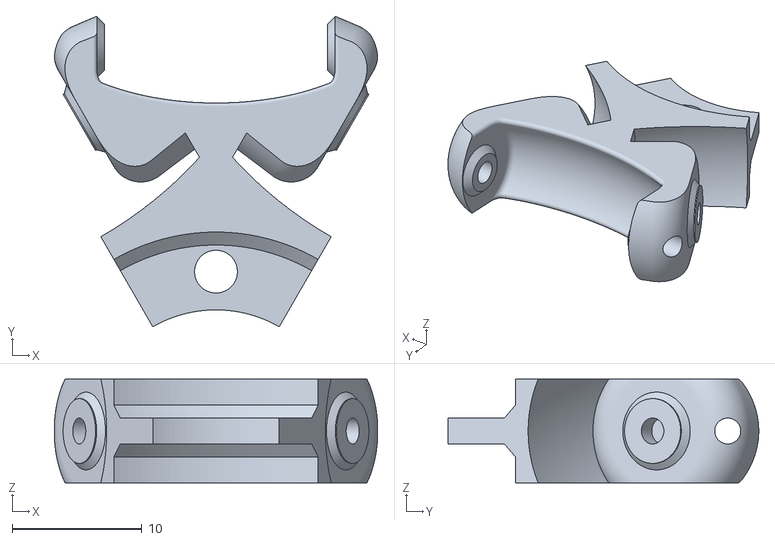
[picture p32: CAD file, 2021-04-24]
mechanical/roda_garfo.STL
24.9 x 24.0 x 8.00

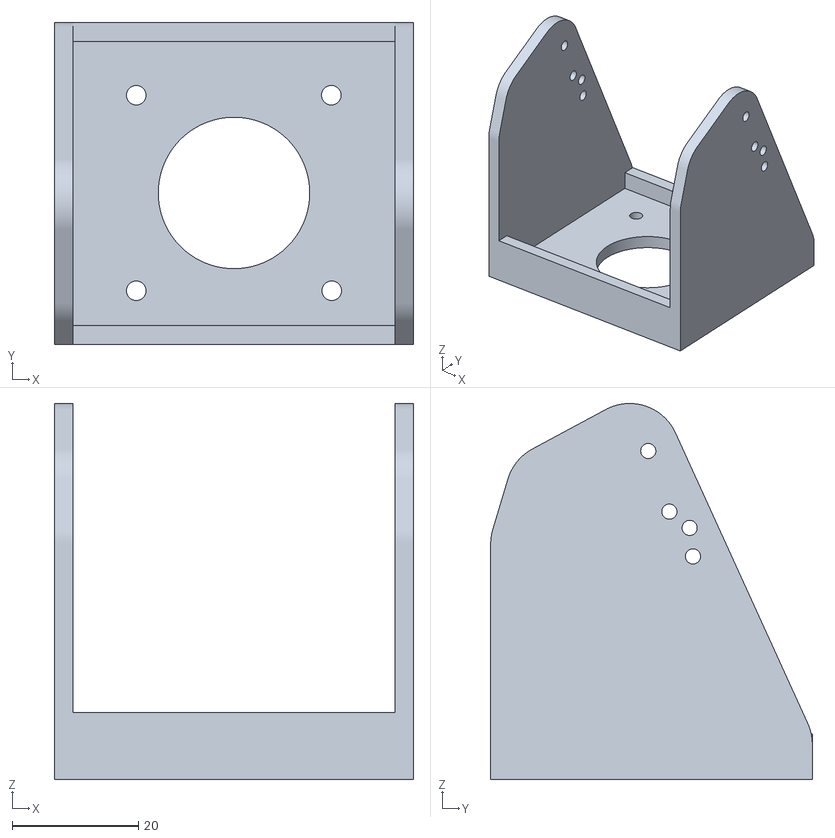
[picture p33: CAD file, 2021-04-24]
mechanical/robo_suporteMotor.STL
57.0 x 51.0 x 59.6

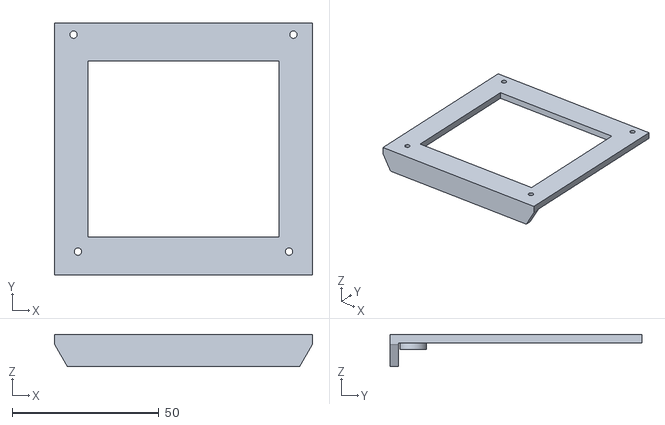
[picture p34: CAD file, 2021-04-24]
mechanical/robo_janela.STL
88.0 x 86.0 x 11.0

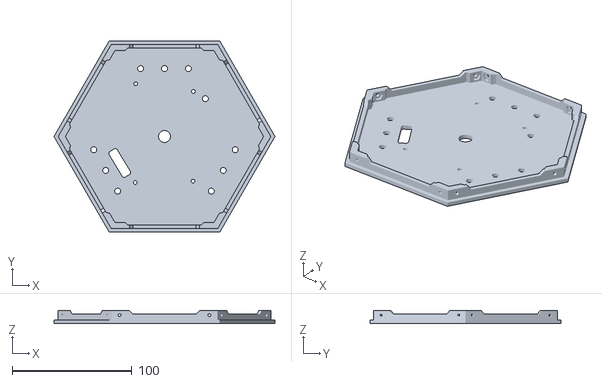
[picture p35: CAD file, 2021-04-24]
mechanical/robo_tampaInferior.STL
184.8 x 160.0 x 11.0

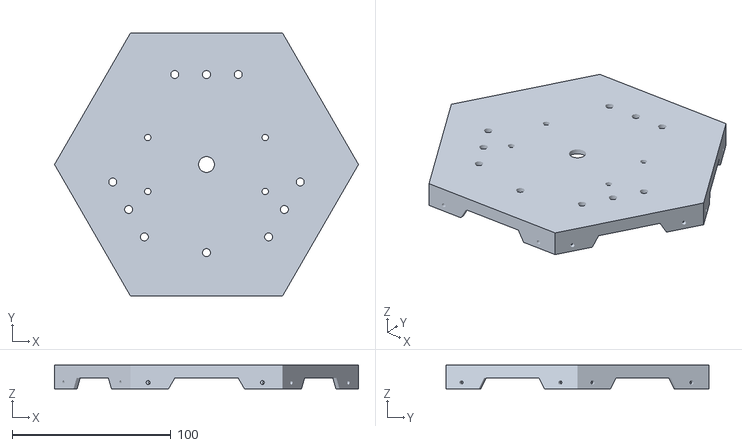
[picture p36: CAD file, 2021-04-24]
mechanical/robo_tampaSuperior.STL
191.7 x 166.0 x 15.0

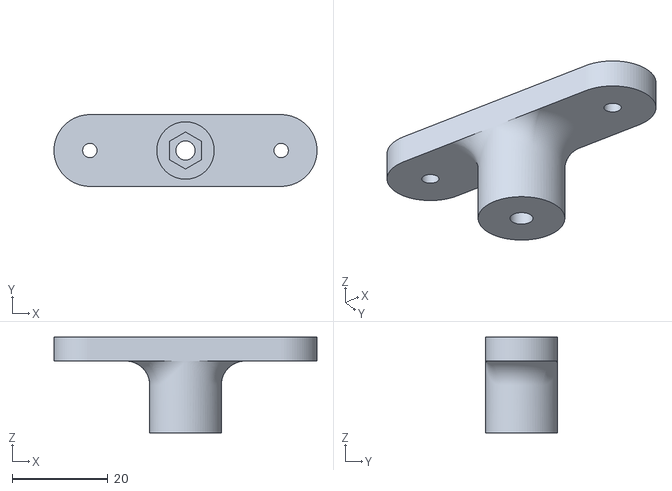
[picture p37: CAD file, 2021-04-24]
mechanical/robo_apoioDisco.STL
55.0 x 15.0 x 20.0

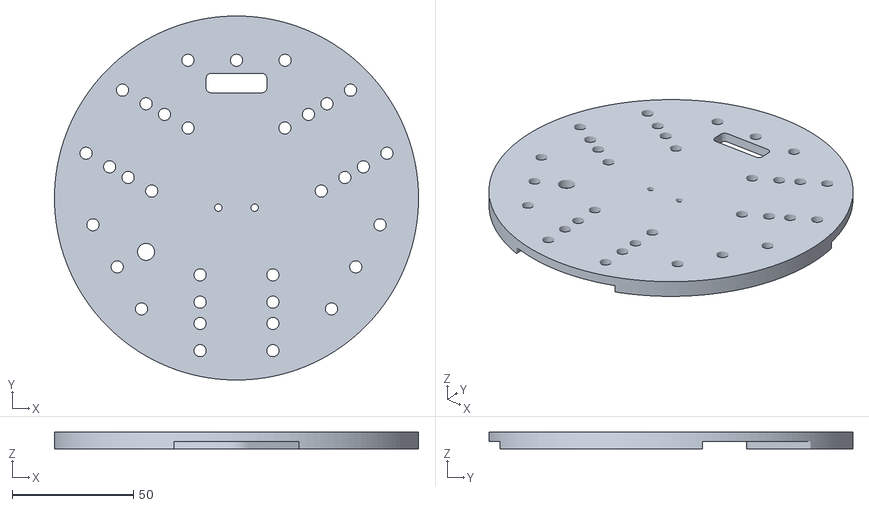
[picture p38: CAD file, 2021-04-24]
mechanical/robo_disco.STL
150.0 x 150.0 x 7.00

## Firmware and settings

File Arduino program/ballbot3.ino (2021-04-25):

// Último teste feito por aqui
#include <Wire.h>
//#include "TimerOne.h"
#include "TimerThree.h"
#include "TimerFour.h"
#include "TimerFive.h"
#include "variaveis.h"
#include <SPI.h>
#include <SD.h>
File myFile;

long periodoLoop=0;
String dados="";
int contDebug=0;

void setup() {
  iniciar(); // configura pinos I/O, configura IMU, bussola, etc
  //iniciarLidar();
  periodoLoop=millis();
}



void loop() {
   
  // Feedback com ângulo e vel. angular (Theta ThetaP)
  ler_IMU(); // ler os angulos e vel. angulares

   
  // Testar em Seno na referência de ângulo do PD (fica muio legal ele fica dançando)
  //SetpointX=sin(millis()*0.004)*refX;
  //SetpointY=sin(millis()*0.01)*refY;
 // SetpointX+=(double)refX;

   // Enviar na Serial b1 (mudar entrada para rampa) ou b0 (para degrau). Padrão é degrau.
   // Ver na aba atuadores, o limite para a rampa parar.
   
   if(tipoEntrada) entradaRampa();
   else entradaDegrau();

   // Enviar na Serial n1 (controle de posição) ou n0 para (controle de velocidade)
   if(modoVelPos==0)  controladorLQRVel(); // Calcula erros e a saída do controlador Velocidade
   if(modoVelPos==1)  controladorLQRPos(); // Calcula erros e a saída do controlador Posição
   
   //controladorPID();  
  // Controle de Guinada
  leituraBussola();  // Obter os valores do magnetômetro
  //imprimeRespostaNatural();
  
  // Modo de ref. do controlador de Guinada 
  //if(contGui>10){
    if(modoGuinada==0)  controladorYawPos(); // Modo de controle de Posição da Guinada (Proporcional)
    if(modoGuinada==1)  controladorYawVel(); // Modo de controle de Velocidade da Guinada (PI)
  //  contGui=0;
  //}
  //contGui++;
  
  // Atuadores 
  converVel(); // Converter velX e velY para M1,M2 e M3 obs rs = radiano/segundo

  setMotor1(M1rs); // ajusta da velocidade do motor 1
  setMotor2(M2rs); // ajusta da velocidade do motor 2
  setMotor3(M3rs); // ajusta da velocidade do motor 3
  
  // Debugguer e telemetria

 debugar(debug);  // Parâmetro debug seleciona quais dados serão impressos na serial


  telemetria();   // Enviar os ângulos para o robô via serial 
  
  // Manter o Loop de controle c/ período constante
  timekeeper();   // Manter o período do loop constante

  Teste_serialEvent3();
}

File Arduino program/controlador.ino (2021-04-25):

void entradaRampa(){

    if( (millis()-tempoRampaVel)>=100 ) {
    SetpointX+=(refX/10); // Criar a rampa com 1/10 da amplitude
    SetpointY+=(refY/10);
    tempoRampaVel=millis();

    
    if( abs(SetpointX)>=(40.0/12) ){
      if(refX>0) SetpointX= 40.0/12;
      if(refX<0) SetpointX=-40.0/12;
    }
    if( abs(SetpointY)>=(40.0/12) ){
      if(refY>0) SetpointY= 40.0/12;
      if(refY<0) SetpointY=-40.0/12;
    }
    
    if(SetpointX>0) SetpointX=0;
    if(SetpointY>0) SetpointY=0;
    
/*
      // Fazer o plato da rampa.
    if( abs(SetpointX)>=(45.0/12) ){
      if(refX>0) SetpointX= 45.0/12;
      if(refX<0) SetpointX=-45.0/12;
    }
  */
   
  }
  
  
}
void entradaDegrau() {

SetpointX=refX;
SetpointY=refY;
/*
  if (SetpointX < refX) SetpointX += 0.03;
  if (SetpointX > refX) SetpointX -= 0.03;
  if (SetpointX == refX) SetpointX = refX;

  if (SetpointY < refY) SetpointY += 0.03;
  if (SetpointY > refY) SetpointY -= 0.03;
  if (SetpointY == refY) SetpointY = refY;
*/
}

void controladorPID() {

/*
refThetaX= (velX - SetpointX)*K3  +  integralErroVelX*K4;
refThetaY= (velY - SetpointY)*K3  +  integralErroVelY*K4;

double anguloMaximo = 2*PI/180;

integralErroVelX += (velX - SetpointX)*elapsedTime;
integralErroVelY += (velY - SetpointY)*elapsedTime;


  // Saturador na saída do controlador
  if (abs(refThetaX) > anguloMaximo) {
    if (refThetaX > 0)refThetaX = anguloMaximo;
    if (refThetaX < 0)refThetaX = -anguloMaximo;
  }
  if (abs(refThetaY) > anguloMaximo) {
    if (refThetaY > 0)refThetaY = anguloMaximo;
    if (refThetaY < 0)refThetaY = -anguloMaximo;
  }


Serial.print(refThetaX);
Serial.print(" , ");
Serial.println(refThetaY);
*/



  // Erro angular
  erroX = (SetpointX-ThetaX);
  erroY = (SetpointY-ThetaY);


  
// Integral do erro de velocidade
integralErroVelX += erroX*elapsedTime;
integralErroVelY += erroY*elapsedTime;

  acelX = (erroX) * K1 + (ThetaXp) * K2 +integralErroVelX*K4;
  acelY = (erroY) * K1 + (ThetaYp) * K2 +integralErroVelY*K4;

  // Saturador na saída do controlador
  if (abs(acelX) > acelMax) {
    if (acelX > 0)acelX = acelMax;
    if (acelX < 0)acelX = -acelMax;
  }
  if (abs(acelY) > acelMax) {
    if (acelY > 0)acelY = acelMax;
    if (acelY < 0)acelY = -acelMax;
  }

  // Velocidade obtida pela integração da aceleração
  velX += acelX * elapsedTime;
  velY += acelY * elapsedTime;

    // Saturador da velocidade dos motores
  if (abs(velX) > freqMax) {
    if (velX > 0)velX = freqMax;
    if (velX < 0)velX = -freqMax;
  }
  if (abs(velY) > freqMax) {
    if (velY > 0)velY = freqMax;
    if (velY < 0)velY = -freqMax;
  }

}

void controladorLQRPos() {


  // Erro angular
  erroX = (0 - ThetaX);
  erroY = (0 - ThetaY);
  erroPosX = (posX - SetpointX);
  erroPosY = (posY - SetpointY);



if(abs(erroX)>5.0*PI/180.0){
  if(erroX>0) erroX= 5.0*PI/180.0;
  if(erroX<0) erroX=-5.0*PI/180.0;
}
if(abs(erroY)>5.0*PI/180.0){
  if(erroY>0) erroY= 5.0*PI/180.0;
  if(erroY<0) erroY=-5.0*PI/180.0;
}

    
  //Converter para centrimetro. Para ficar mais intuitivo
  // Vezes raio 0.12 daria metro, vezes 100 p/ cm então multiplicar por 12.
  // Se aplicar ref. de 5000 o erro será muito alto, saturar em um erro máximo de 30 cm.


// Erro muito grande pode provocar queda, então abaixo é feito um saturador no erro
  if(tipoEntrada==0){

    // Frente é diferente da ré, por isso saturar diferente.
    if( (erroPosX*12)>12) { 
        erroPosX=12.0/12.0;
    }
     if( (erroPosX*12)<-30) { 
        erroPosX=-30.0/12.0;
    }
    
    // Saturador de Y é igual pq é simétrico o movimento esquerda e direita
    if( abs(erroPosY*18)>20) { 
        if(erroPosY>0) erroPosY= 18.0/12.0;
        if(erroPosY<0) erroPosY=-18.0/12.0;
    } 

  //Serial.println(erroPosX*12.0);
 }


 
  //if( abs(erroPosX*12)<5 && abs(erroPosY*12)<5 ) {  K4 = 0;  } 
  //else {   K4 = 2;       }

  
//if( abs(erroPosX*12)<20  &&  abs(erroPosY*12)<20) {K4=1;Serial.println("Perto");}
  //else {K4=1.5;Serial.println("Longe");}
  
  
  // Aceleração (Saída do controlador)
  acelX = (erroX) * K1 + (ThetaXp) * K2 +  (velX) * K3  +  erroPosX* K4;
  acelY = (erroY) * K1 + (ThetaYp) * K2 +  (velY) * K3  +  erroPosY* K4;

  
  /*
    // Filtro na saída do controlador
    acelX = acelXAnt*0.5 + acelX*0.5;
    acelY = acelYAnt*0.5 + acelY*0.5;
    acelXAnt =acelX;
    acelYAnt =acelY;
  */

  // Saturador na saída do controlador
  if (abs(acelX) > acelMax) {
    if (acelX > 0)acelX = acelMax;
    if (acelX < 0)acelX = -acelMax;
  }

  if (abs(acelY) > acelMax) {
    if (acelY > 0)acelY = acelMax;
    if (acelY < 0)acelY = -acelMax;
  }

  // Velocidade obtida pela integração da aceleração
  velX += acelX * elapsedTime;
  velY += acelY * elapsedTime;


  // Posição obtida pela integração da velocidade
  posX += velX * elapsedTime;
  posY += velY * elapsedTime;


 // posX = posX*0.8+posXAnt*0.2;
 // posY = posY*0.8+posYAnt*0.2;
  //posXAnt=posX; posYAnt=posY; // Salvar as posições anteriores
     
  // Saturador da velocidade dos motores
  if (abs(velX) > freqMax) {
    if (velX > 0)velX = freqMax;
    if (velX < 0)velX = -freqMax;
  }
  if (abs(velY) > freqMax) {
    if (velY > 0)velY = freqMax;
    if (velY < 0)velY = -freqMax;
  }


}

void controladorLQRVel() {

double erroVelX=0;
double erroVelY=0;

 // Erro angular
  erroX = (0 - ThetaX);
  erroY = (0 - ThetaY);

erroVelX = velX - SetpointX;
erroVelY = velY - SetpointY;
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
